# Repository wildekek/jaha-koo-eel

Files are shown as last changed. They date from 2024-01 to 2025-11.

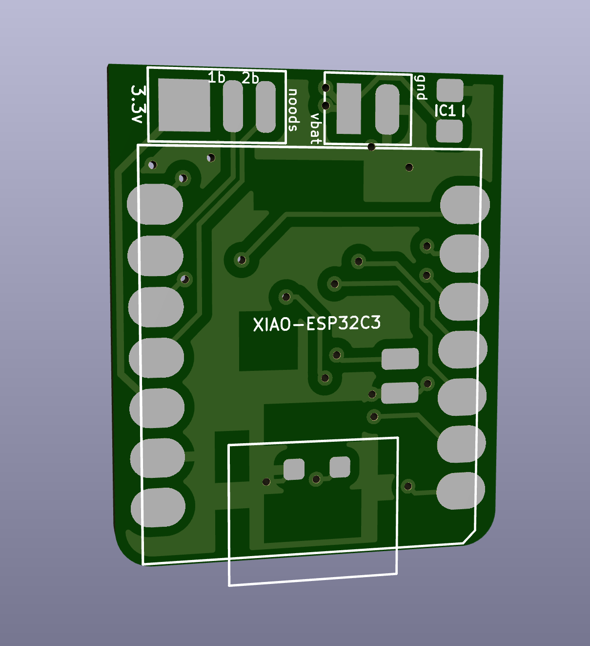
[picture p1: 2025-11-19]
kicad/eel_head_pcbs_assembly/eel_esp32_switch_host_board_v02/_export/images/HariboKimchi Eel mainboard - front.png

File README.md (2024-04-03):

# Jaha Koo Eel

A robotic remote controlled eel. A prop for the play [Haribo Kimchi](https://www.campo.nu/en/production/24342/haribo_kimchi).

A collaboration between [Adriaan Wormgoor](http://adriaanwormgoor.nl) and [Willem Vooijs](https://willem.vooijs.eu), produced for [Stichting Theater Utrecht](https://www.theaterutrecht.nl/innovationlab) and [Campo](https://campo.nu).

haribo

## Build your own
[Bill of Materials](./BOM.md)

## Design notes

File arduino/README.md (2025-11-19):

# Arduino code

All sketches where developed in `VSCode` using the `Platformio` extension.

There's a _lot_ of scrappy test sketches, so find below a quick link to the most recent version of key sketches.

### Main sketch for Eel microcontroller (XIAO ESP32-C3)

[main_seeed_xiao_esp32c3_v2_w_external_files.cpp](./platformio/esp32c3_helloworld/esp32c3_helloworld/src/main_seeed_xiao_esp32c3_v2_w_external_files.cpp)

### Main sketch for Teensy 3.2 inside the GEPRC Tinyradio r/c transmitter

[main.cpp](./platformio/TeensyDuino/src/main.cpp)

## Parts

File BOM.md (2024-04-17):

# Bill Of Materials

## 3Print files

> 💡 Print all these files in PETG

| Quantity | Model | Color |
| --- | --- | --- |
| 1 | Motor Mount | Transparent  |
| 1 | Head Upper | Transparent  |
| 1 | Head Lower | Transparent  |
| 1 | Switch cap | Transparent  |
| 2 | Eye Light Guide | Black |
| 2 | Mouth Light Guide | Black |
| 2 | Front Wheel | Transparent  |
| 1 | Tail | Transparent  |
| 19 | Segment | Transparent  |
| 8 | Segment with n00d | Transparent  |
| 1 | Segment battery | Transparent  |
| 4 | Axle | Transparent  |
| 8 | Wheel | Transparent  |

## Components

| Quantity | Component | Comments |
| --- | --- | --- |
| 8 | O-ring for wheels | Transparent silicone  |
| 2 | O-ring for front wheels | Transparent silicone  |

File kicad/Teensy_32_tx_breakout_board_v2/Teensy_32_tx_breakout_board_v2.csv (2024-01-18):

Source: | /Users/adriaanwormgoor/datkanarie/projects/Theater Utrecht - Jaha Koo Eel/Jaha Koo Eel - git/kicad/Teensy_32_tx_breakout_board/Teensy_32_tx_breakout_board.kicad_sch
Date: | 2024 January 09, Tuesday 16:21:45
Tool: | Eeschema (6.0.5-0)
Generator: | /Applications/KiCad/KiCad.app/Contents/SharedSupport/plugins/bom_csv_grouped_by_value_with_fp.py
Component Count: | 11
Ref | Qnty | Value | Cmp name | Footprint | Description | Vendor
C1, C2, C3, | 3 | 1uf | C | Capacitor_SMD:C_0603_1608Metric | Unpolarized capacitor
J1, J2, J3, J4, | 4 | Conn_01x03_Female | Conn_01x03_Female | Connector_JST:JST_SH_BM03B-SRSS-TB_1x03-1MP_P1.00mm_Vertical | Generic connector, single row, 01x03, script generated (kicad-library-utils/schlib/autogen/connector/)
R1, R2, R3, | 3 | 10k | R | Resistor_SMD:R_0603_1608Metric | Resistor
U1, | 1 | Teensy3.2_backpack | Teensy3.2_backpack | teensy_library-master:Teensy30_31_32_outside_pins

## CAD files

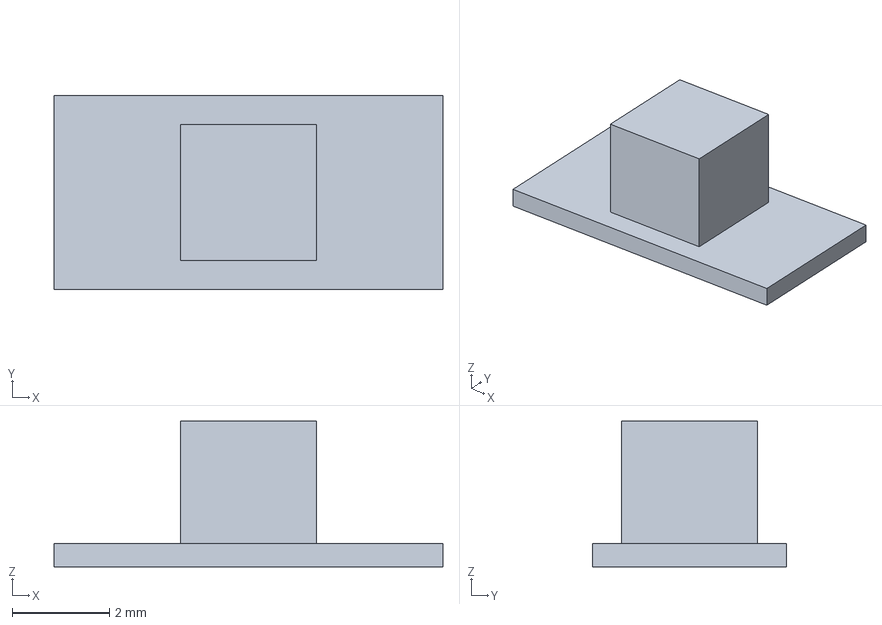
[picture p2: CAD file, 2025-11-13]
CAD/3mf/Main pcb slide switch end cap.3mf
8.00 x 4.00 x 3.00 mm

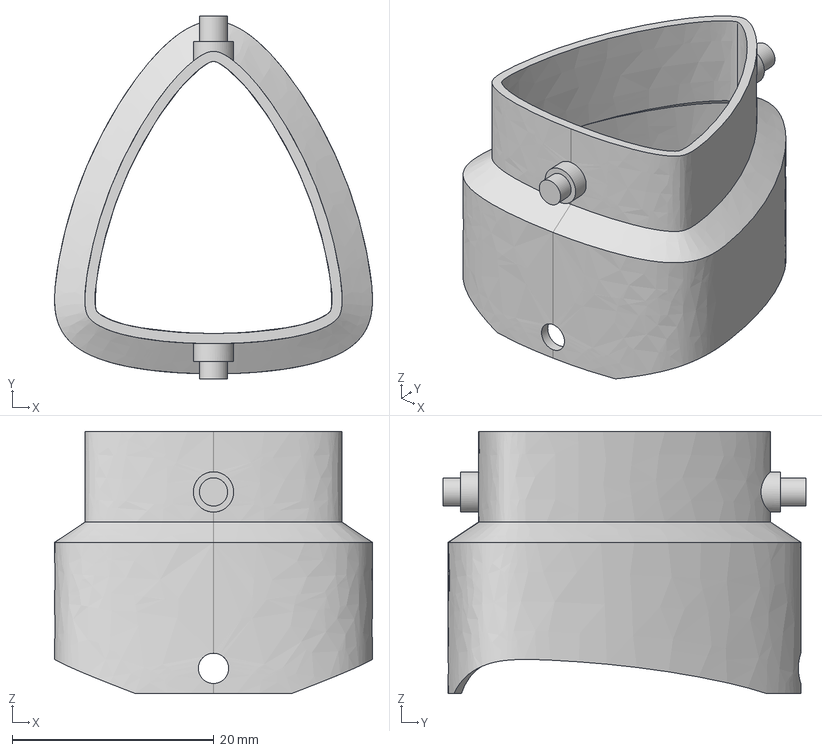
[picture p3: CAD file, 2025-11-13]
CAD/Haribo.step
31.5 x 36.0 x 26.0 mm

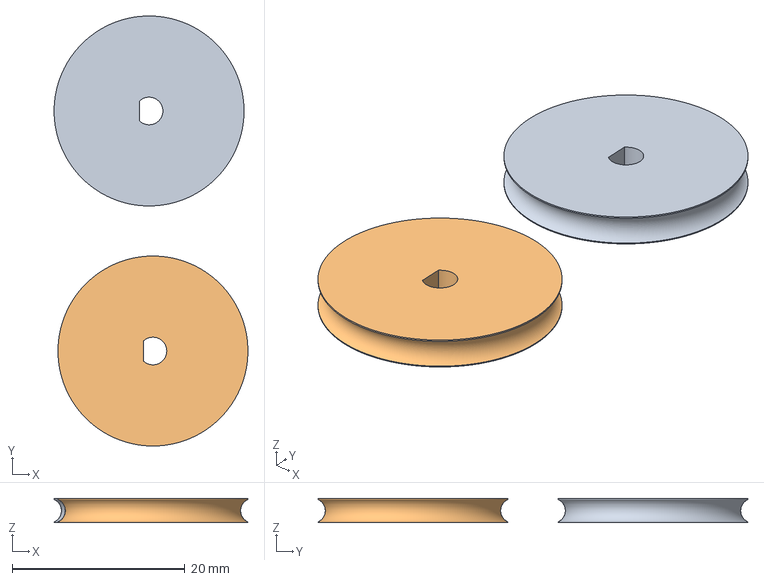
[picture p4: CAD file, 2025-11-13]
CAD/3mf/motor wheel v01.3mf
22.4 x 49.8 x 2.80 mm

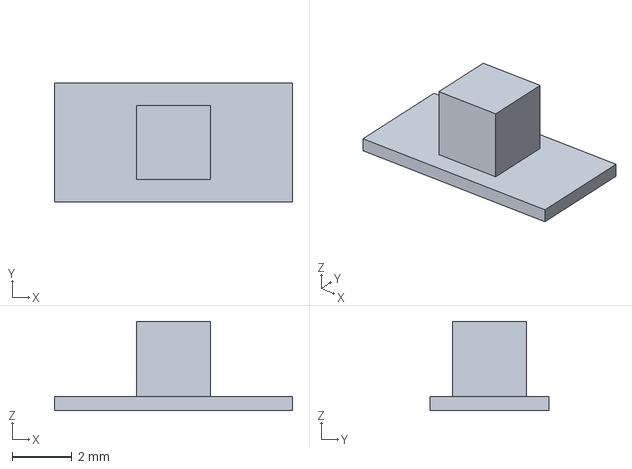
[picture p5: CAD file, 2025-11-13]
CAD/3mf/Switch cap .3mf
8.00 x 4.00 x 3.00 mm

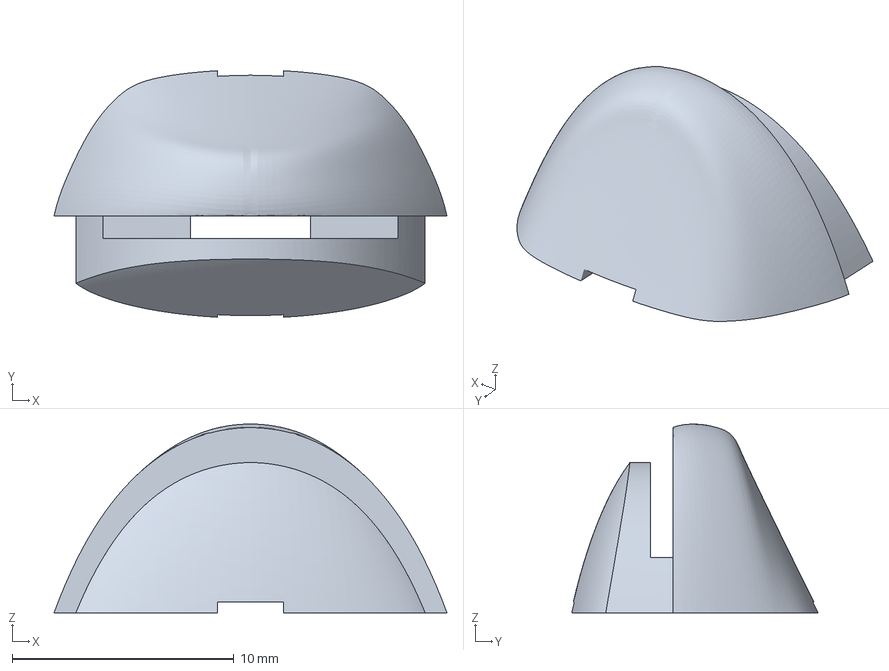
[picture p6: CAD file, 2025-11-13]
CAD/3mf/Mouth Light Guide.3mf
17.7 x 11.1 x 8.52 mm

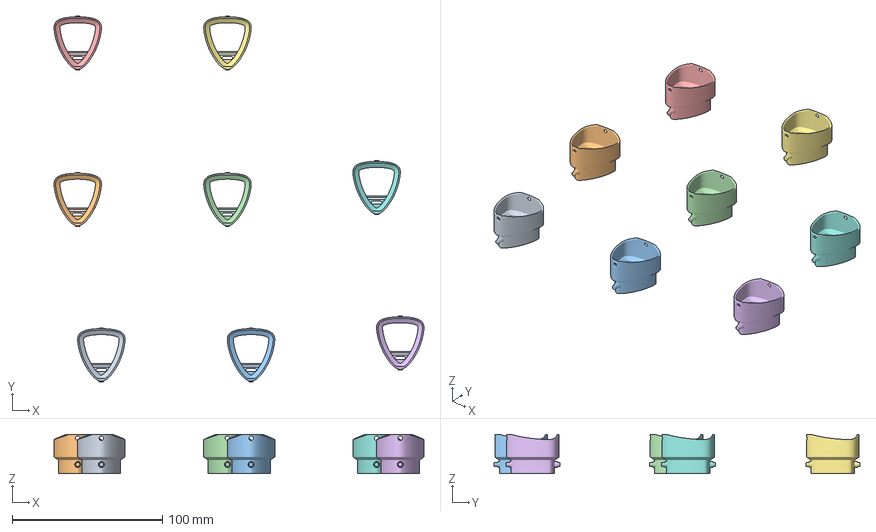
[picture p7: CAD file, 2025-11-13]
CAD/3mf/Segment with n00d.3mf
246.0 x 243.3 x 26.0 mm
Segment (1)
Segment (1) 1 x 2
Segment (1) 2
Segment (1) 3
Segment (1) 4
Segment (1) 5
Segment (1) 6

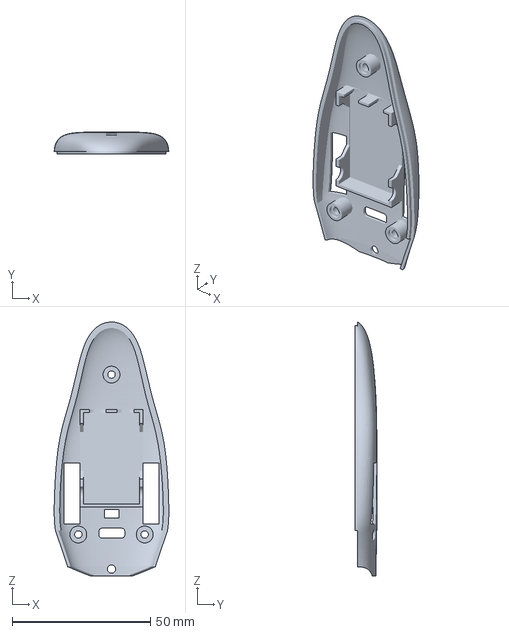
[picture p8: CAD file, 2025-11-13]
CAD/3mf/Head Lower.3mf
41.4 x 8.04 x 91.8 mm

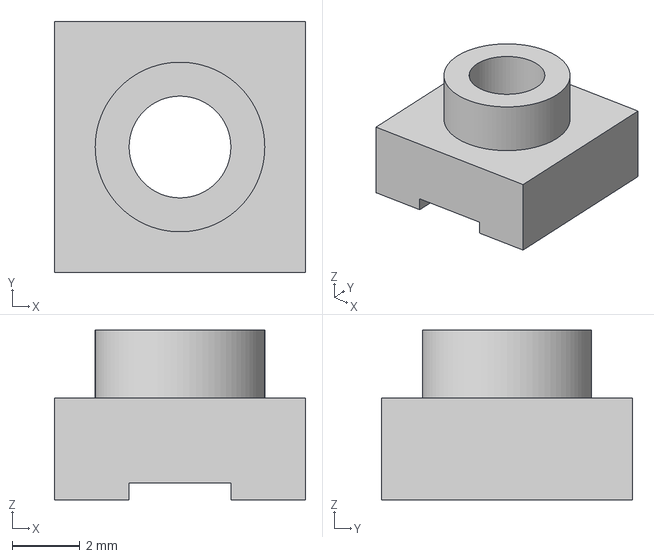
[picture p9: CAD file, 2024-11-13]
CAD/3mf/Eye Light Guide.3mf
7.40 x 7.40 x 5.00 mm

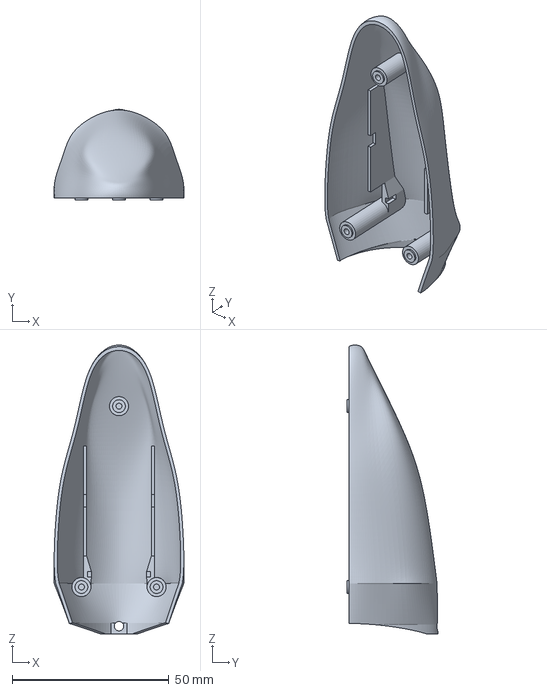
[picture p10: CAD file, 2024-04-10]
CAD/3mf/Head Upper.3mf
41.5 x 28.9 x 92.3 mm

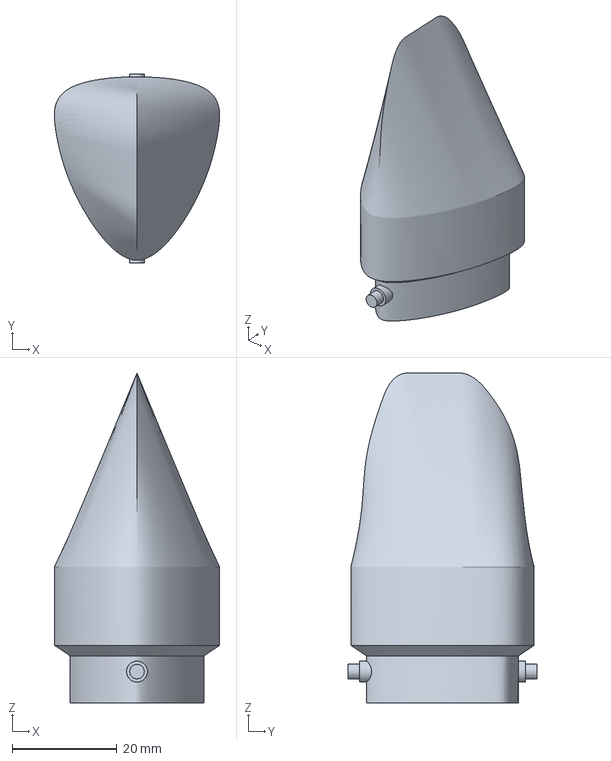
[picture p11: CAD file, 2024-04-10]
CAD/3mf/Tail.3mf
31.5 x 36.0 x 63.0 mm

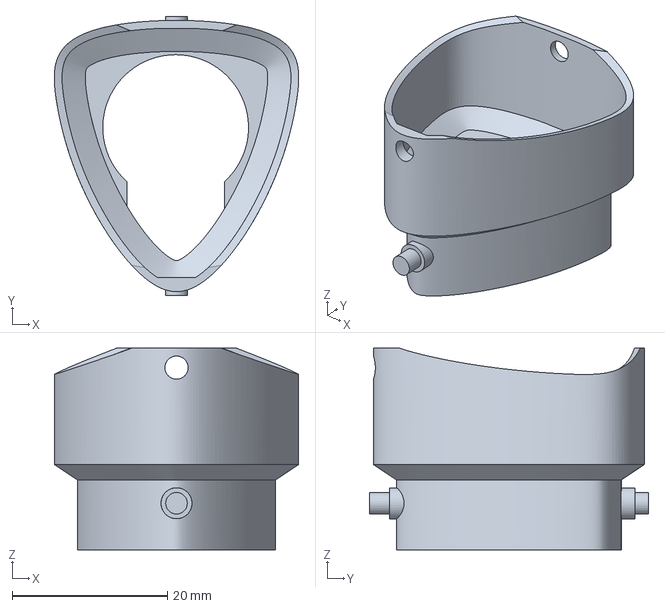
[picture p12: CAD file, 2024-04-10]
CAD/3mf/Segment Battery.3mf
31.5 x 36.0 x 26.0 mm

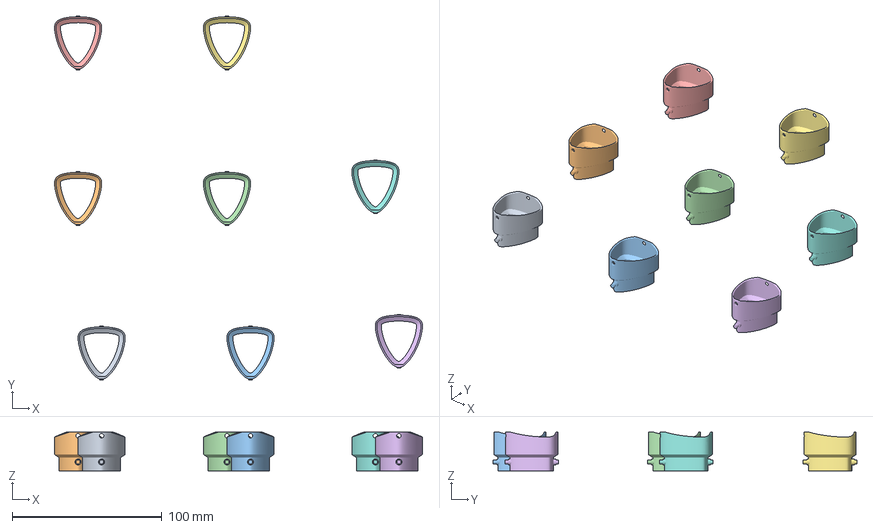
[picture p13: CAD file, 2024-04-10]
CAD/3mf/Segment.3mf
246.0 x 243.3 x 26.0 mm
Segment (1)
Segment (1) 1
Segment (1) 2
Segment (1) 3
Segment (1) 4
Segment (1) 5
Segment (1) 6
Segment (1) 7

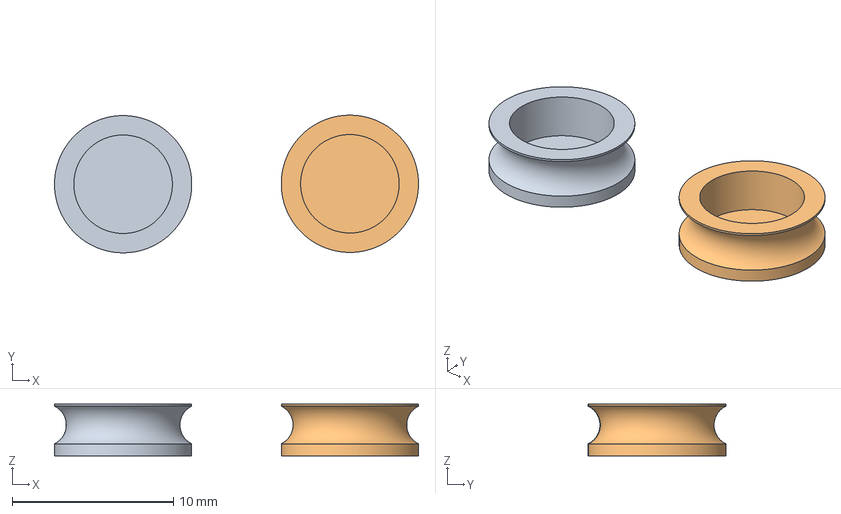
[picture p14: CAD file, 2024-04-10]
CAD/3mf/undercarriage wheel.3mf
22.5 x 8.53 x 3.20 mm
ball bearing wheel cover (with o-ring slot) v07 slightly tighter (2024-04-08).stl x 2

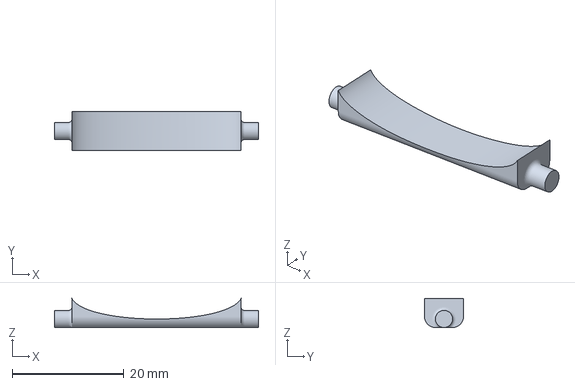
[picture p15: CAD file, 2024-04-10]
CAD/3mf/undercarriage axle.3mf
36.5 x 7.00 x 5.20 mm

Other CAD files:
CAD/3mf/Motor Mount.3mf

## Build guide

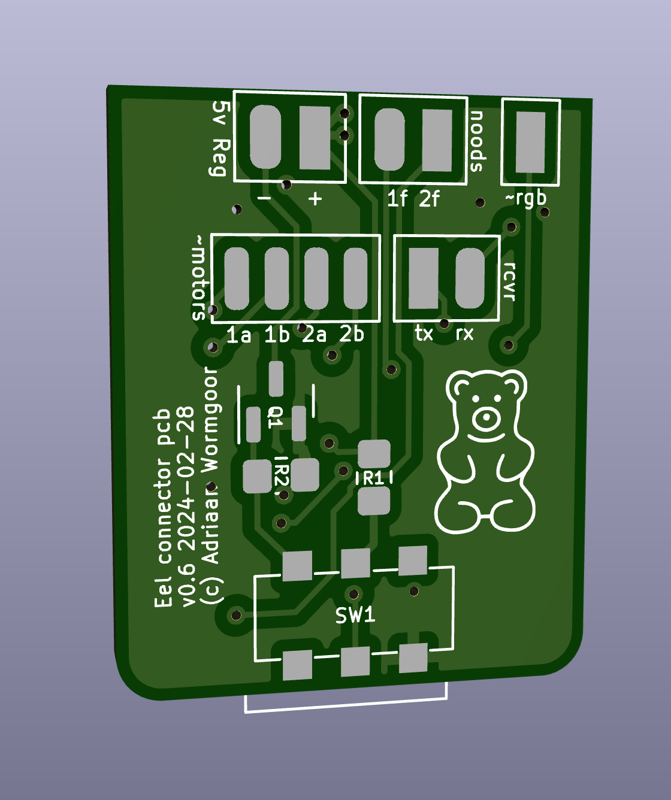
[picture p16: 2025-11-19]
kicad/eel_head_pcbs_assembly/eel_esp32_switch_host_board_v02/_export/images/HariboKimchi Eel mainboard - back.png

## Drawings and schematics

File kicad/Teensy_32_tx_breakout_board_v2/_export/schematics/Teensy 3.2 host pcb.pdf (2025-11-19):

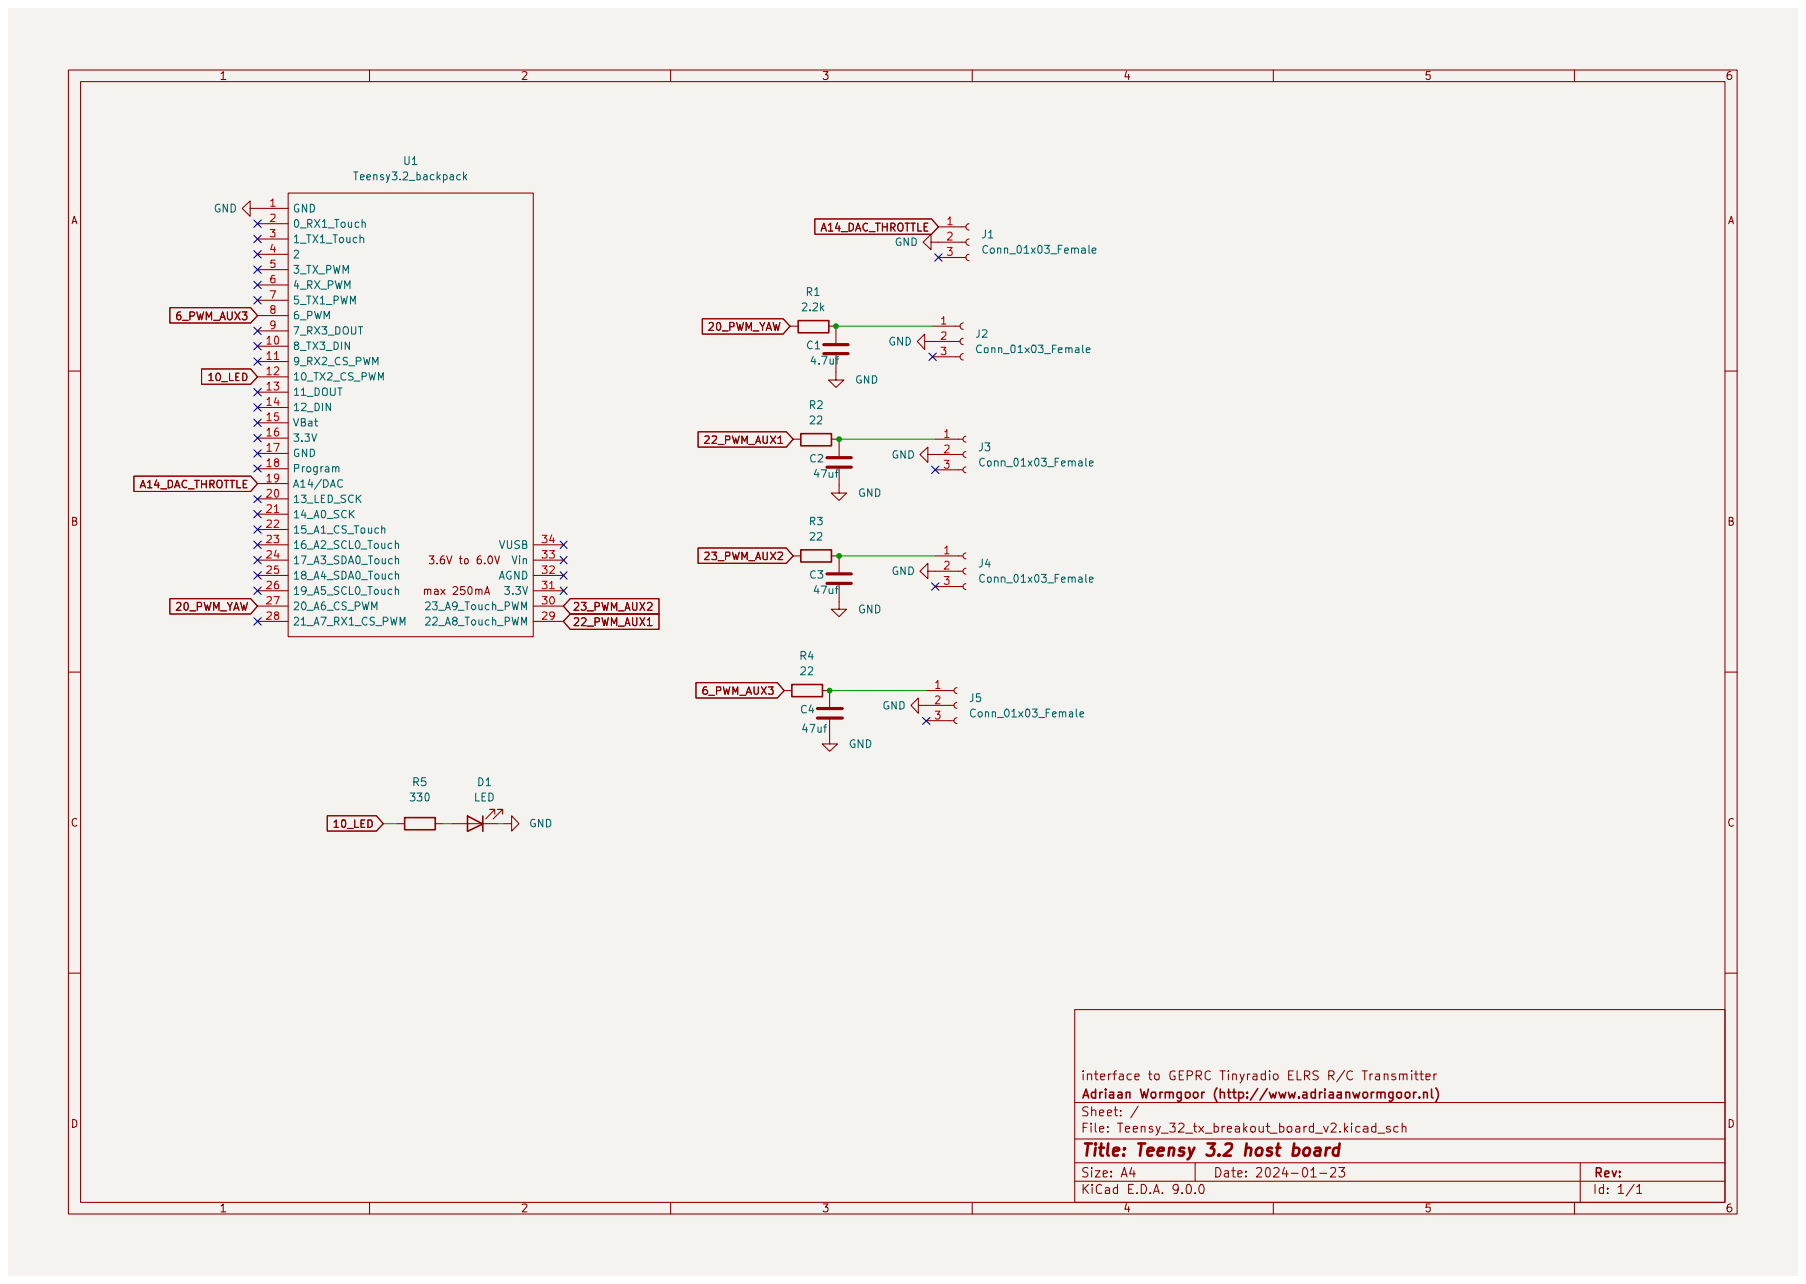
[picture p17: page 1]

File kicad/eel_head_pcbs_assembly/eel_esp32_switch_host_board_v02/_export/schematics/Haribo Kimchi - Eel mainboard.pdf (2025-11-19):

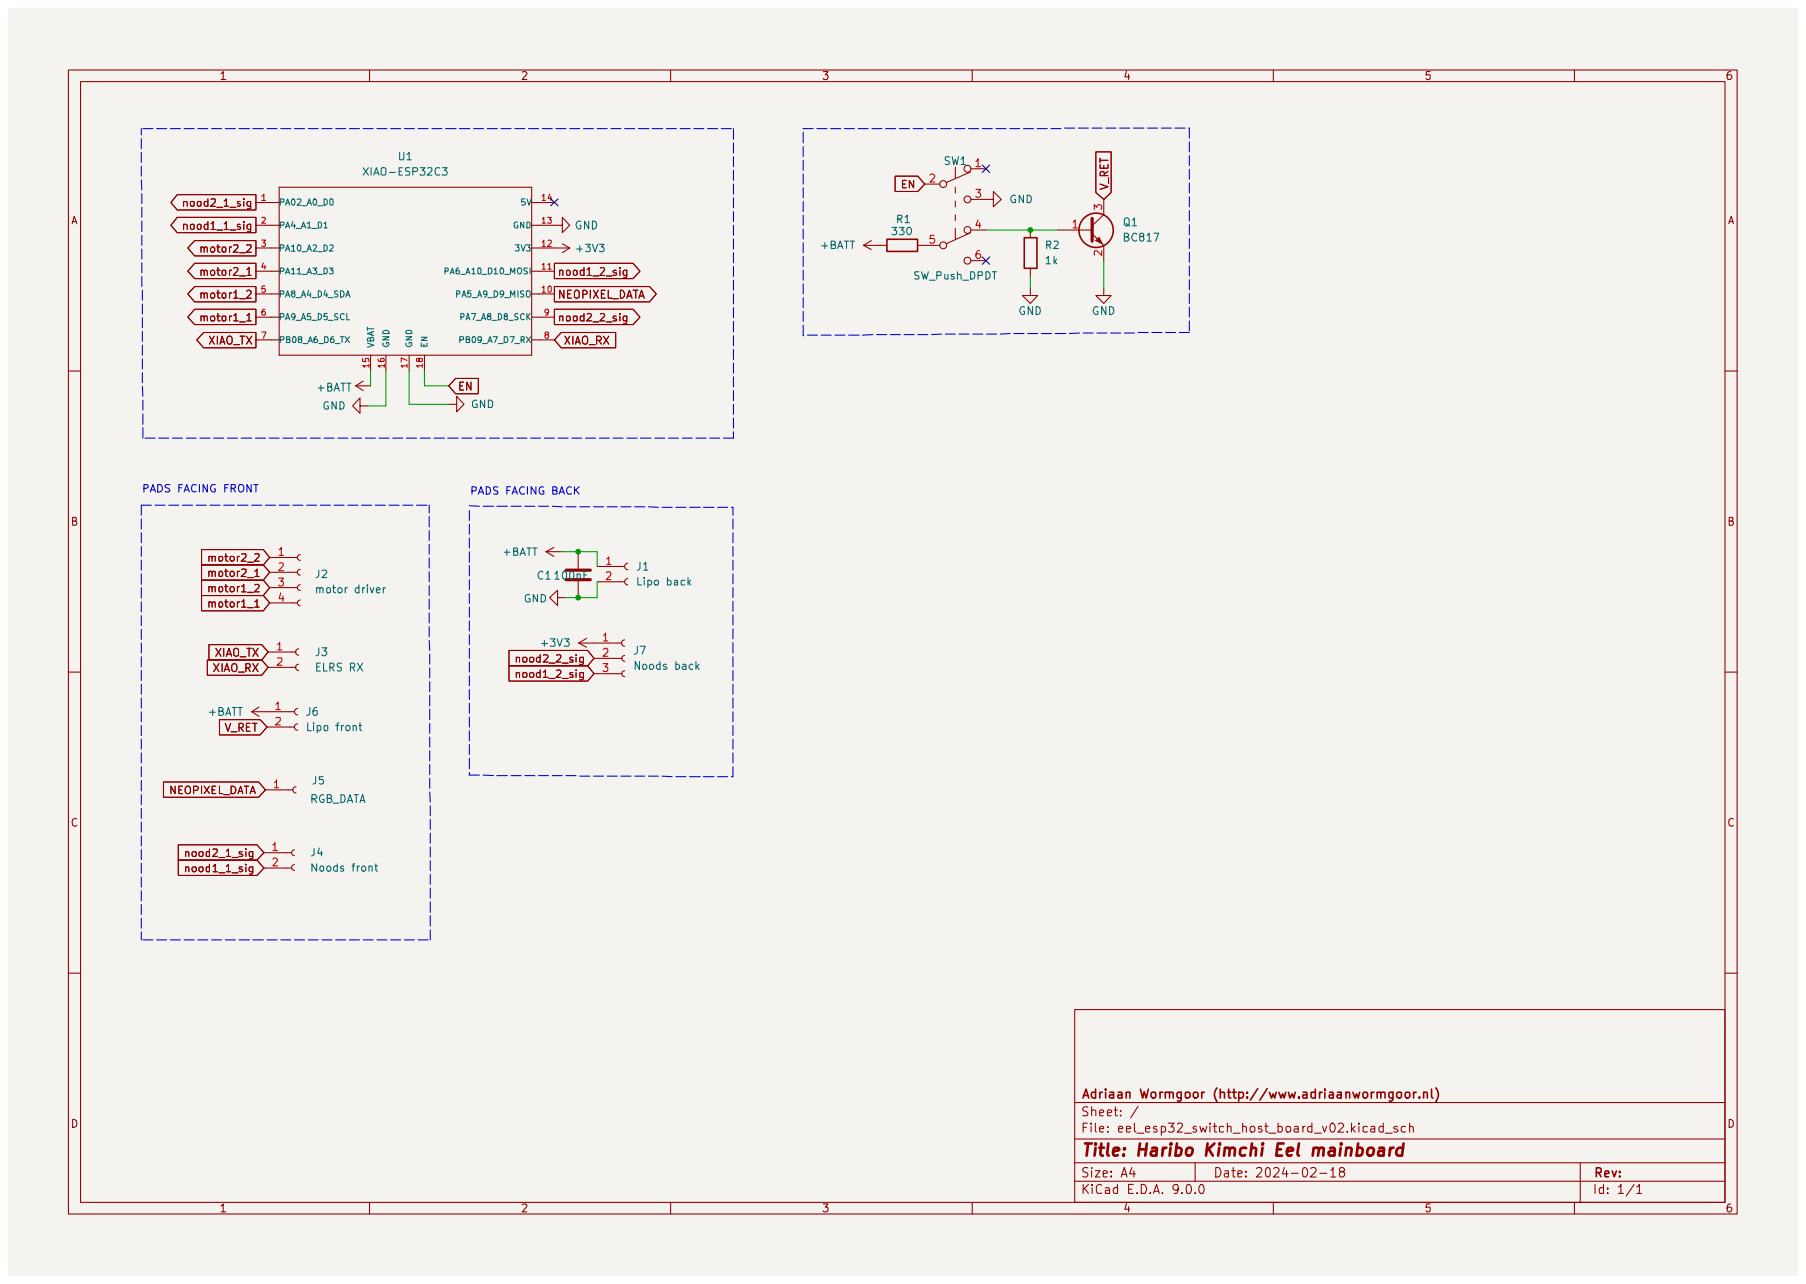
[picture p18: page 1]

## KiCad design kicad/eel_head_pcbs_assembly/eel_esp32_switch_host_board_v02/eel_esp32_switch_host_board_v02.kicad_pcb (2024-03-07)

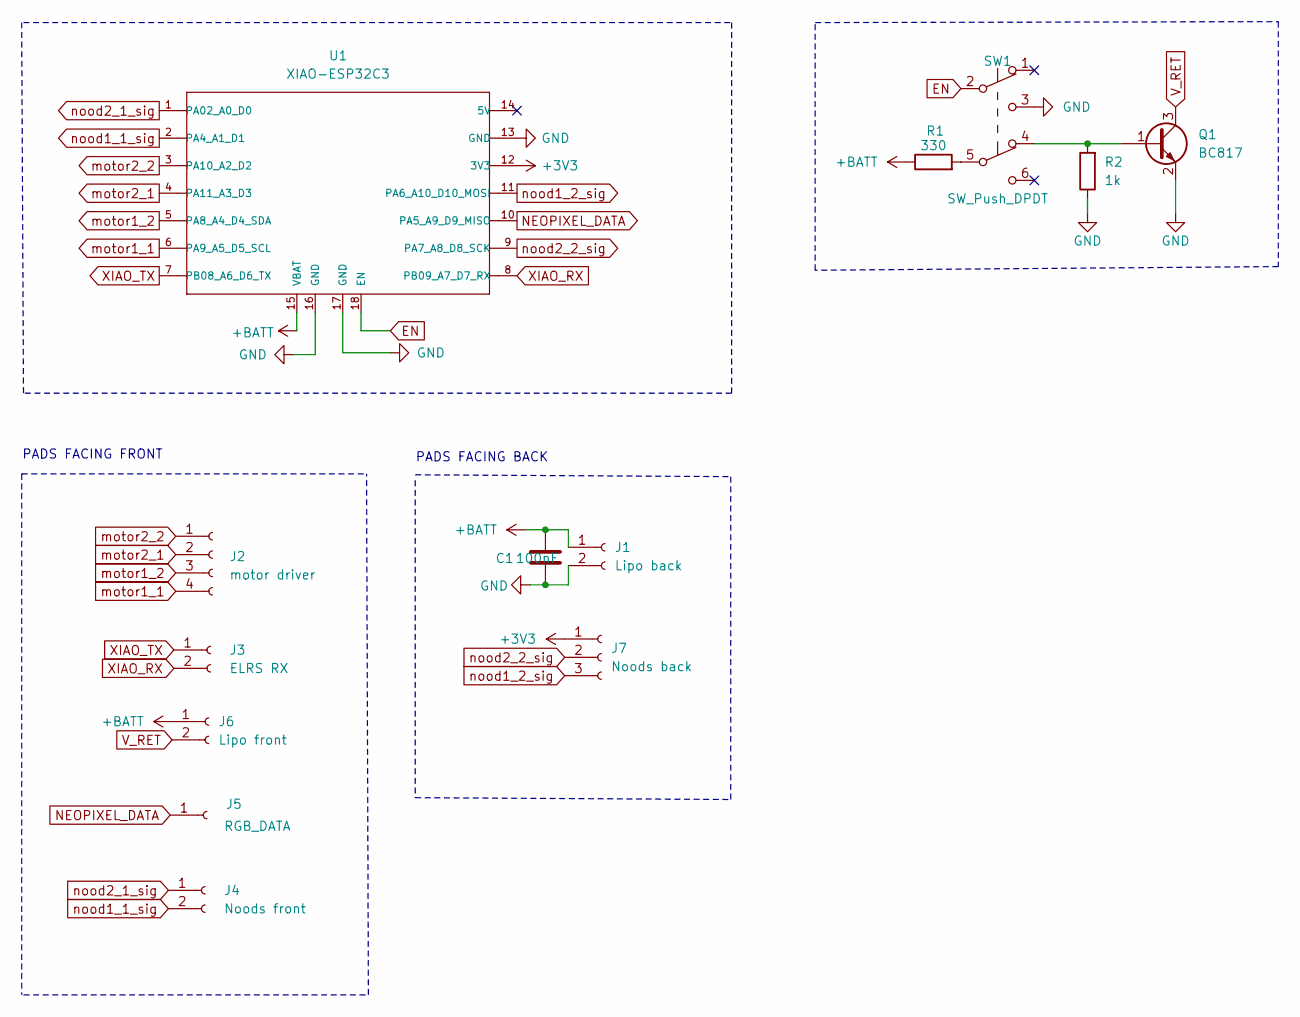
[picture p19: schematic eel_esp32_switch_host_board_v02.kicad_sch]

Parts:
C1: 100nF; C_0805_2012Metric_Pad1.18x1.45mm_HandSolder
J1: Lipo back; smd_solder_pads_1x02_2.54mm
J2: motor driver; smd_solder_pads_1x04
J3: ELRS RX; smd_solder_pads_1x02_2.54mm
J4: Noods front; smd_solder_pads_1x02_2.54mm
J5: RGB_DATA; smd_solder_pads_1x01_2.54mm
J6: Lipo front; smd_solder_pads_1x02_2.54mm
J7: Noods back; smd_solder_pads_1x03_n00ds_v1
Q1: BC817; SOT-23
R1: 330; R_0805_2012Metric_Pad1.20x1.40mm_HandSolder
R2: 1k; R_0805_2012Metric_Pad1.20x1.40mm_HandSolder
SW1: SW_Push_DPDT; Nidec_2x03_dpdt_CL-SB-22B-11
U1: XIAO-ESP32C3; MOUDLE14P-SMD-2.54-21X17.8MM

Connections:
+3V3: J7.1, U1.12 (3V3)
+BATT: C1.1, J1.1, J6.1, R1.1, U1.15 (VBAT)
EN: SW1.2 (B), U1.18 (EN)
GND: C1.2, J1.2, Q1.2 (E), R2.1, SW1.3 (C), U1.13 (GND), U1.16 (GND), U1.17 (GND)
NEOPIXEL_DATA: J5.1, U1.10 (PA5_A9_D9_MISO)
unnamed: Q1.1 (B), R2.2, SW1.4 (A)
unnamed: R1.2, SW1.5 (B)
V_RET: J6.2, Q1.3 (C)
XIAO_RX: J3.2, U1.8 (PB09_A7_D7_RX)
XIAO_TX: J3.1, U1.7 (PB08_A6_D6_TX)
motor1_1: J2.4, U1.6 (PA9_A5_D5_SCL)
motor1_2: J2.3, U1.5 (PA8_A4_D4_SDA)
motor2_1: J2.2, U1.4 (PA11_A3_D3)
motor2_2: J2.1, U1.3 (PA10_A2_D2)
nood1_1_sig: J4.2, U1.2 (PA4_A1_D1)
nood1_2_sig: J7.3, U1.11 (PA6_A10_D10_MOSI)
nood2_1_sig: J4.1, U1.1 (PA02_A0_D0)
nood2_2_sig: J7.2, U1.9 (PA7_A8_D8_SCK)

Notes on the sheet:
PADS FACING BACK
PADS FACING FRONT

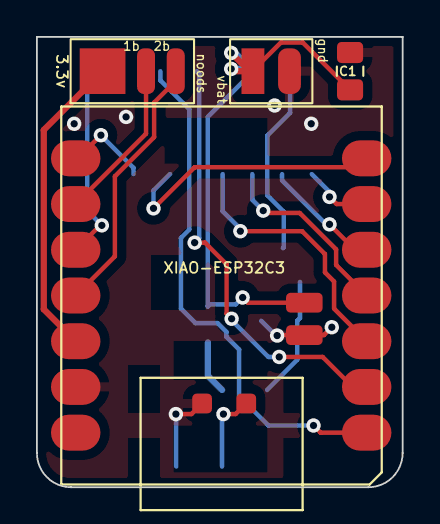
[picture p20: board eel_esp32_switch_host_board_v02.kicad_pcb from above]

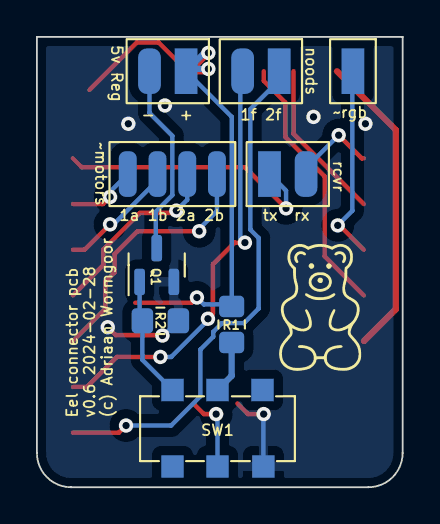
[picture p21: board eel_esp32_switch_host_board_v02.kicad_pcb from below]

Board: 2 copper layers, 20.3 x 25.0 mm, 13 parts (9 on the bottom side), 18 nets.

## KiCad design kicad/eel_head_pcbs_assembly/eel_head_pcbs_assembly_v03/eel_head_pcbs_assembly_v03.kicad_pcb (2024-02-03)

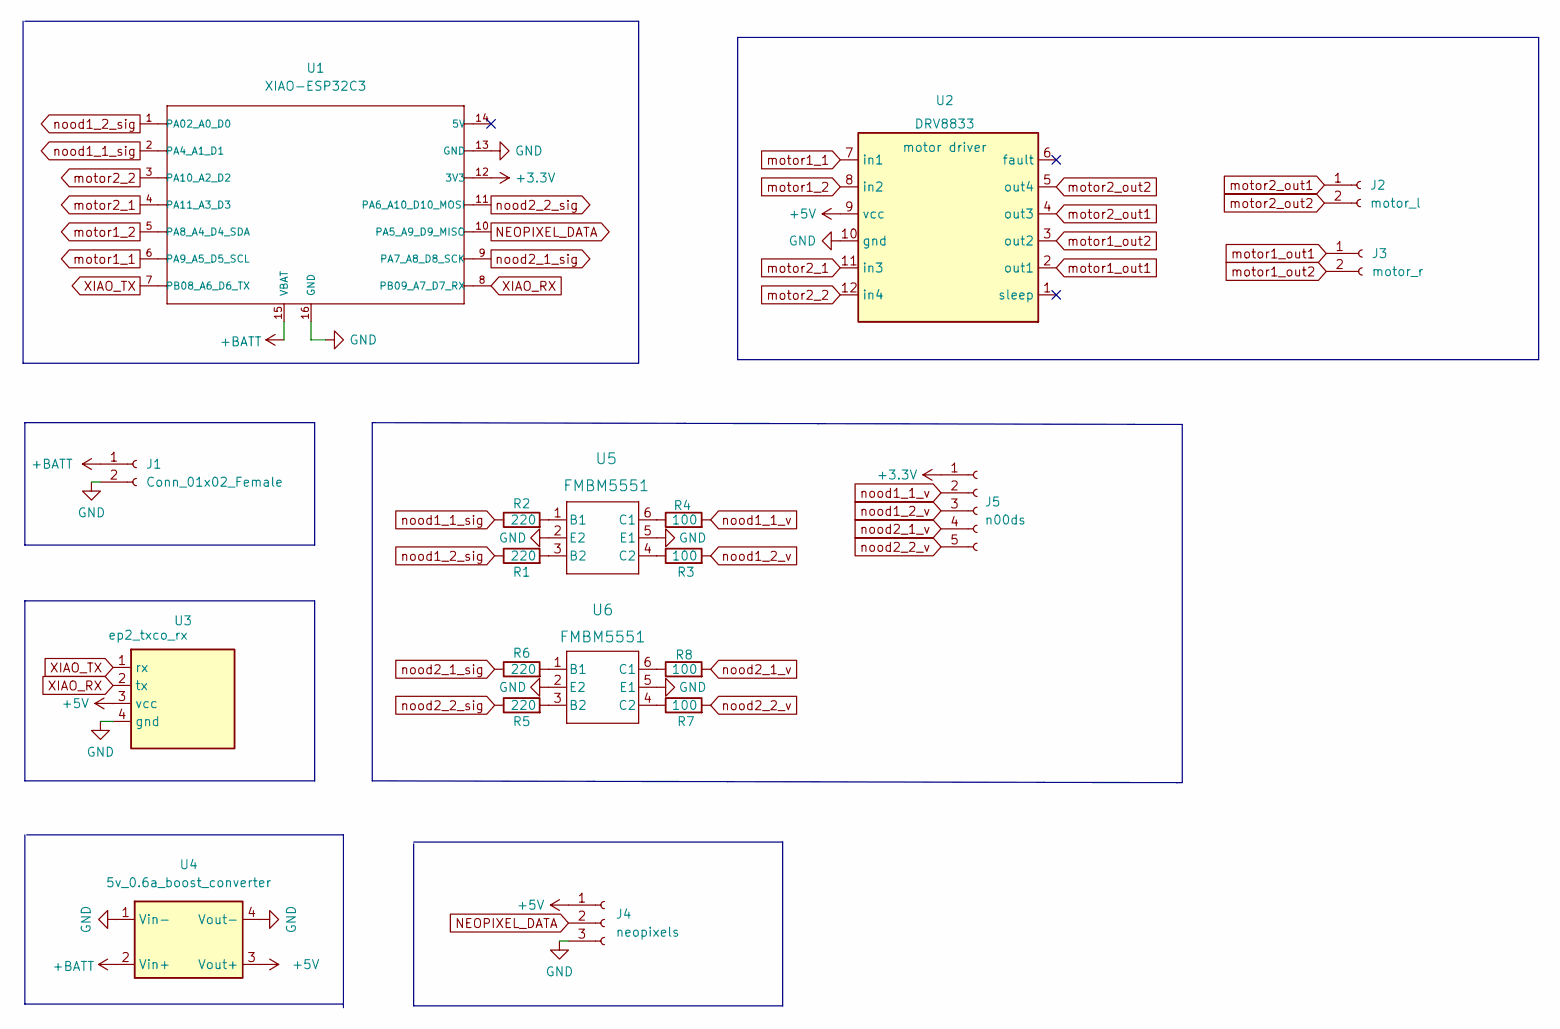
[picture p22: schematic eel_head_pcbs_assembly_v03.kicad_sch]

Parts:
J1: Conn_01x02_Female; JST_PH_S2B-PH-K_1x02_P2.00mm_Horizontal
J2: motor_l; smd_solder_pads_1x02_2.54mm
J3: motor_r; smd_solder_pads_1x02_2.54mm
J4: neopixels; smd_solder_pads_1x03_2.54mm
J5: n00ds; smd_solder_pads_1x05_n00ds_v2_smaller
R1, R2, R5, R6: 220; R_0603_1608Metric_Pad0.98x0.95mm_HandSolder
R3, R4, R7, R8: 100; R_0603_1608Metric_Pad0.98x0.95mm_HandSolder
U1: XIAO-ESP32C3; MOUDLE14P-SMD-2.54-21X17.8MM
U2: DRV8833; drv8833_breakout
U3: ep2_txco_rx; happymodel_ep2_txco_rx
U4: 5v_0.6a_boost_converter
U5, U6: FMBM5551; SSOT6_3X1P7_ONS

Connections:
+3V3: J5.1, U1.12 (3V3)
+5V: J4.1, U2.9 (vcc), U3.3 (vcc), U4.3 (Vout+)
+BATT: J1.1, U1.15 (VBAT), U4.2 (Vin+)
GND: J1.2, J4.3, U1.13 (GND), U1.16 (GND), U2.10 (gnd), U3.4 (gnd), U4.1 (Vin-), U4.4 (Vout-), U5.2 (E2), U5.5 (E1), U6.2 (E2), U6.5 (E1)
NEOPIXEL_DATA: J4.2, U1.10 (PA5_A9_D9_MISO)
unnamed: R1.2, U5.3 (B2)
unnamed: R2.2, U5.1 (B1)
unnamed: R3.1, U5.4 (C2)
unnamed: R4.1, U5.6 (C1)
unnamed: R5.2, U6.3 (B2)
unnamed: R6.2, U6.1 (B1)
unnamed: R7.1, U6.4 (C2)
unnamed: R8.1, U6.6 (C1)
XIAO_RX: U1.8 (PB09_A7_D7_RX), U3.2 (tx)
XIAO_TX: U1.7 (PB08_A6_D6_TX), U3.1 (rx)
motor1_1: U1.6 (PA9_A5_D5_SCL), U2.7 (in1)
motor1_2: U1.5 (PA8_A4_D4_SDA), U2.8 (in2)
motor1_out1: J3.1, U2.2 (out1)
motor1_out2: J3.2, U2.3 (out2)
motor2_1: U1.4 (PA11_A3_D3), U2.11 (in3)
motor2_2: U1.3 (PA10_A2_D2), U2.12 (in4)
motor2_out1: J2.1, U2.4 (out3)
motor2_out2: J2.2, U2.5 (out4)
nood1_1_sig: R2.1, U1.2 (PA4_A1_D1)
nood1_1_v: J5.2, R4.2
nood1_2_sig: R1.1, U1.1 (PA02_A0_D0)
nood1_2_v: J5.3, R3.2
nood2_1_sig: R6.1, U1.9 (PA7_A8_D8_SCK)
nood2_1_v: J5.4, R8.2
nood2_2_sig: R5.1, U1.11 (PA6_A10_D10_MOSI)
nood2_2_v: J5.5, R7.2

Board: 2 copper layers, 21 parts (15 on the bottom side), 31 nets, no tracks yet.

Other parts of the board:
haribo_korean: LOGO; haribo_in_korean_3.2mm
logo_haribo_bear: LOGO; haribo_outline_bw_8mm

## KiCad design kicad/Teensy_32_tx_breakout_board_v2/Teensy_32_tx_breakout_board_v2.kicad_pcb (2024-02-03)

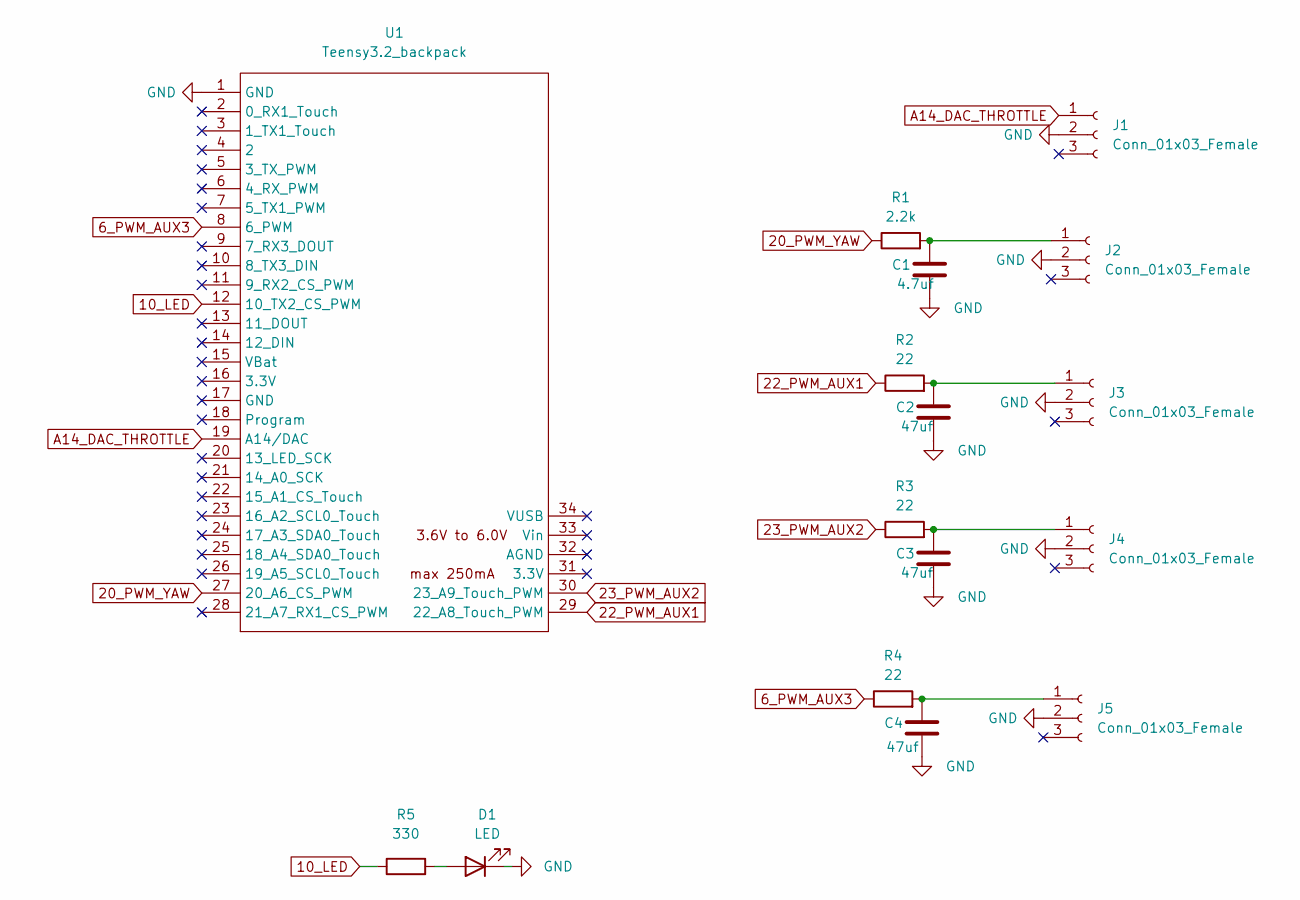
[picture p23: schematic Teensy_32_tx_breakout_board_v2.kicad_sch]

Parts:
C1: 4.7uf; C_0603_1608Metric
C2, C3, C4: 47uf; C_0603_1608Metric
D1: LED; LED_1206_3216Metric
J1, J2, J3, J4, J5: Conn_01x03_Female; JST_SH_BM03B-SRSS-TB_1x03-1MP_P1.00mm_Vertical
R1: 2.2k; R_0603_1608Metric
R2, R3, R4: 22; R_0603_1608Metric
R5: 330; R_1206_3216Metric
U1: Teensy3.2_backpack; Teensy30_31_32_outside_pins

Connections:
6_PWM_AUX3: R4.1, U1.8 (6_PWM)
10_LED: R5.1, U1.12 (10_TX2_CS_PWM)
20_PWM_YAW: R1.1, U1.27 (20_A6_CS_PWM)
22_PWM_AUX1: R2.1, U1.29 (22_A8_Touch_PWM)
23_PWM_AUX2: R3.1, U1.30 (23_A9_Touch_PWM)
A14_DAC_THROTTLE: J1.1, U1.19 (A14/DAC)
GND: C1.2, C2.2, C3.2, C4.2, D1.2 (K), J1.2, J2.2, J3.2, J4.2, J5.2, U1.1 (GND)
unnamed: C1.1, J2.1, R1.2
unnamed: C2.1, J3.1, R2.2
unnamed: C3.1, J4.1, R3.2
unnamed: C4.1, J5.1, R4.2
unnamed: D1.1 (A), R5.2

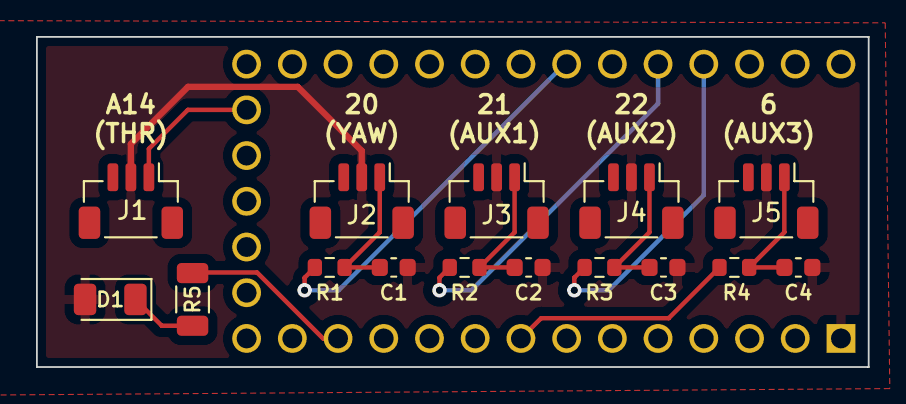
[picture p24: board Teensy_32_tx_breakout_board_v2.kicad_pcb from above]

Board: 2 copper layers, 46.2 x 18.3 mm, 16 parts (1 on the bottom side), 12 nets.

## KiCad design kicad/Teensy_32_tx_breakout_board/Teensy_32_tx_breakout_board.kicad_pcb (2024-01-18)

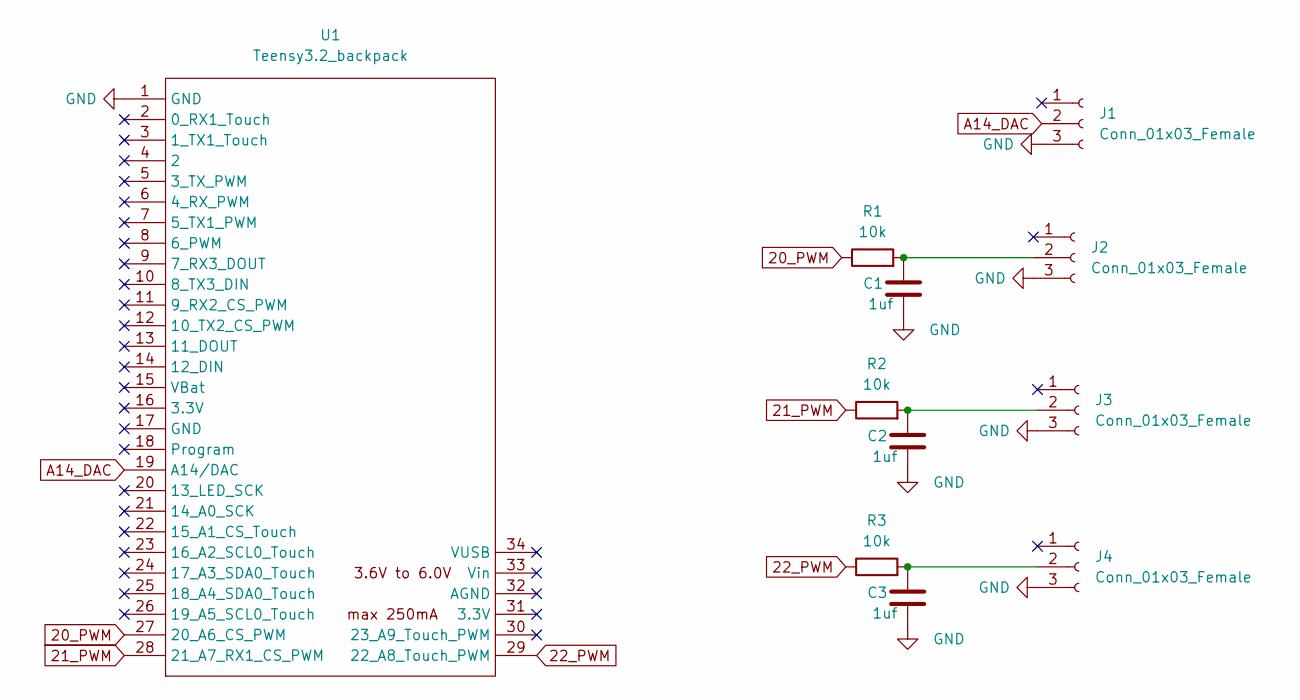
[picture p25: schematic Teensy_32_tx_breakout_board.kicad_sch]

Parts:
C1, C2, C3: 1uf; C_0603_1608Metric
J1, J2, J3, J4: Conn_01x03_Female; JST_SH_BM03B-SRSS-TB_1x03-1MP_P1.00mm_Vertical
R1, R2, R3: 10k; R_0603_1608Metric
U1: Teensy3.2_backpack; Teensy30_31_32_outside_pins

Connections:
20_PWM: R1.1, U1.27 (20_A6_CS_PWM)
21_PWM: R2.1, U1.28 (21_A7_RX1_CS_PWM)
22_PWM: R3.1, U1.29 (22_A8_Touch_PWM)
A14_DAC: J1.2, U1.19 (A14/DAC)
GND: C1.2, C2.2, C3.2, J1.3, J2.3, J3.3, J4.3, U1.1 (GND)
unnamed: C1.1, J2.2, R1.2
unnamed: C2.1, J3.2, R2.2
unnamed: C3.1, J4.2, R3.2

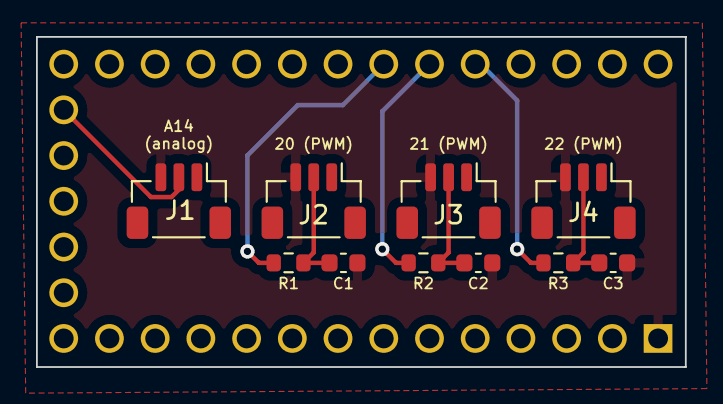
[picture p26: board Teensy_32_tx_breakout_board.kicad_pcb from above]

Board: 2 copper layers, 36.1 x 18.3 mm, 11 parts (1 on the bottom side), 8 nets.

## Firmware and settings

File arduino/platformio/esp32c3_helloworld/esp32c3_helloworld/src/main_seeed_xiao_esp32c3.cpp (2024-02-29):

#include <Arduino.h>
#include <EelMotor.h>
#include <Wire.h>
#include "sbus.h"
#include <HardwareSerial.h>
#include <Adafruit_NeoPixel.h>
#include <FastLED.h>

// NeoPixel
#define PIN D9
#define NUMPIXELS 3

// When setting up the NeoPixel library, we tell it how many pixels,
// and which pin to use to send signals. Note that for older NeoPixel
// strips you might need to change the third parameter -- see the
// strandtest example for more information on possible values.
Adafruit_NeoPixel pixels(NUMPIXELS, PIN, NEO_GRB + NEO_KHZ800);

HardwareSerial MySerial0(0);

/* SBUS object, reading SBUS */
bfs::SbusRx sbus_rx(&MySerial0, D7, D6, true, false);

/* SBUS data */
bfs::SbusData data;

#define motor1a_pin D5
#define motor1b_pin D4
#define motor2a_pin D3
#define motor2b_pin D2

#define motor1_chan 4 // 6 Channels (ESP32-C3) (0-5) are availible
#define motor2_chan 5 // 6 Channels (ESP32-C3) (0-5) are availible

// setting PWM properties
const uint32_t freq = 2500;
const uint8_t resolution = 8;

EelMotor motor1(motor1a_pin, motor1b_pin, motor1_chan, resolution, freq);
EelMotor motor2(motor2a_pin, motor2b_pin, motor2_chan, resolution, freq);

u_long sbusPrevPacketTime;
bool sbusLost = false;

#define SBUS_VAL_MIN 191
#define SBUS_VAL_MAX 1793
#define SBUS_VAL_CENTER 992
#define SBUS_VAL_DEADBAND 6
#define SBUS_LOST_TIMEOUT 100
#define SBUS_SWITCH_MIN 192
#define SBUS_SWITCH_MAX 1792
#define SBUS_SWITCH_MIN_THRESHOLD 1400
#define SBUS_SWITCH_MAX_THRESHOLD 550

#define TX_ROLL 0
#define TX_PITCH 1
#define TX_THROTTLE 2
#define TX_YAW 3
#define TX_AUX1 4
#define TX_AUX2 5
#define TX_AUX3 6
#define TX_AUX4 7

enum HEAD_STATE
{
  STATE_1,
  STATE_2
};
HEAD_STATE headState = STATE_1;

enum BODY_STATE
{
  NOOD1,
  NOOD2,
  BOTH_NOODS
};
BODY_STATE bodyState = BOTH_NOODS;

// The CONNECTION_ESTABLISHED and CONNECTION_LOST states are kind of vanity states, in case I want to
// implement some kind of unique visual feedback for when the connection is lost or established.
enum CONNECTION_STATE
{
  DISCONNECTED,
  CONNECTION_ESTABLISHED,
  CONNECTION_LOST,
  CONNECTED
};
CONNECTION_STATE connectionState = DISCONNECTED;

#define SBUS_PACKET_PRINT_INTERVAL 100 // ms
u_long sbusPacketPrintPrevTime = 0;

float sinCounter = 0.0;
float sinCounterIncrement = 0.05;

bool doSineMovement = false;

byte hVal = 0;
byte vVal = 0;

int16_t motor1Val;
int16_t motor2Val;

int16_t n00d1a, n00d1b, n00d2a, n00d2b;
uint16_t throttle, throttleAdjusted;

int16_t noodVals[] = {0, 0, 0, 0};
int16_t noodAvgVals[] = {0, 0, 0, 0};
uint16_t n00dSegmentIdentifiers[] = {512, 640, 768, 896};

#define n00d_1a_Pin D1
#define n00d_1b_Pin D10
#define n00d_2a_Pin D0
#define n00d_2b_Pin D8

static const uint8_t nood1a_chan = 0;
static const uint8_t nood1b_chan = 1;
static const uint8_t nood2a_chan = 2;
static const uint8_t nood2b_chan = 3;

void initNoods();
void initPixels();
void updateBodyValues();
void updateBodyLighting();
void updateSerialIO();
void checkIncomingSerial();
void setn00d(uint8_t chan, uint8_t val);

void resetSbusData();
void setLights_disconnected();

// define methods
void driveMotors();
void parseSBUS(bool serialPrint);
void updateHeadBodyState();
void updateHeadLighting();
void updateBodyLighting();
void calcMotorValues();

void setup()
{
  Serial.begin(115200);

  /* Begin the SBUS communication */
  sbus_rx.Begin();
  // sbus_tx.Begin();

  /* not sure if this is necessary...
  ledcDetachPin(n00d_1a_Pin);
  ledcDetachPin(n00d_1b_Pin);
  ledcDetachPin(motor1a_pin);
  ledcDetachPin(motor1a_pin);
  ledcDetachPin(motor1b_pin);
  ledcDetachPin(motor2a_pin);
  ledcDetachPin(motor2b_pin);
  //*/

  initNoods();

  motor1.reversed = true;
  motor2.reversed = false;

  // by default, let's have the program assume sbus is lost
  sbusPrevPacketTime = -SBUS_LOST_TIMEOUT;

  initPixels();

  Serial.println("Hello World!");
}

void loop()
{
  // pixels.clear(); // Set all pixel colors to 'off'

  // read SBUS
  parseSBUS(true);

  // determine how to set the head and body lights
  switch (connectionState) {
    case DISCONNECTED:
      resetSbusData();
      setLights_disconnected();
      break;
    case CONNECTION_ESTABLISHED:
      if (sbusLost) {
        connectionState = CONNECTION_LOST;
      } else {
        connectionState = CONNECTED;
      }
      break;
    case CONNECTION_LOST:
      if (!sbusLost) {
        connectionState = CONNECTION_ESTABLISHED;
      }
      break;
    case CONNECTED:
      if (sbusLost) {
        connectionState = CONNECTION_LOST;
      }
      break;
  }

  updateHeadBodyState();

  updateBodyValues();
  updateBodyLighting();

  updateHeadLighting();
  // updateBodyLighting();

  calcMotorValues();
  driveMotors();

  // delay a little.
  delay(1000 / 200);
}

void initNoods()
{
  pinMode(n00d_1a_Pin, OUTPUT);
  pinMode(n00d_1b_Pin, OUTPUT);
  pinMode(n00d_2a_Pin, OUTPUT);
  pinMode(n00d_2b_Pin, OUTPUT);

  // nood 1a
  ledcSetup(nood1a_chan, freq, resolution);
  ledcAttachPin(n00d_1a_Pin, nood1a_chan);

  // nood 1b
  ledcSetup(nood1b_chan, freq, resolution);
  ledcAttachPin(n00d_1b_Pin, nood1b_chan);

  // nood 2a
  ledcSetup(nood2a_chan, freq, resolution);
  ledcAttachPin(n00d_2a_Pin, nood2a_chan);

  // nood 2b
  ledcSetup(nood2b_chan, freq, resolution);
  ledcAttachPin(n00d_2b_Pin, nood2b_chan);

  setn00d(nood1a_chan, 0);
  setn00d(nood1b_chan, 0);
  setn00d(nood2a_chan, 0);
  setn00d(nood2b_chan, 0);
}

void initPixels() {
  pixels.begin(); // INITIALIZE NeoPixel strip object (REQUIRED)
  delay(10);
  pixels.clear();
  pixels.show();
}

void updateBodyValues()
{
  // map throttle range to 0-1023
  throttle = map(data.ch[TX_THROTTLE], SBUS_VAL_MIN, SBUS_VAL_MAX, 0, 1023);

  throttleAdjusted = 0; // used to store the adjusted throttle value

  // if (throttle & (0x1 << 9)) // 512
  // if (throttle & n00dSegmentIdentifiers[0] == n00dSegmentIdentifiers[0]) // 512
  if (throttle >> 7 == 0x4) // 0b100
  {
    // throttleAdjusted = throttle - (throttle >> 5);
    throttleAdjusted = throttle - 9;
    n00d1a = (throttle & 0x7E) - 9;
    n00d1a = map(constrain(n00d1a, 0, 55), 0, 55, 0, 255);
  }
  // if (throttle & (0x1 << 8)) // 256
  // if (throttle & n00dSegmentIdentifiers[1] == n00dSegmentIdentifiers[1]) // 640
  if (throttle >> 7 == 0x5) // 0b101
  {
    // throttle -= throttle - (throttle >> 5);
    throttleAdjusted = throttle - 10;
    n00d1b = (throttle & 0x7E) - 10;
    n00d1b = map(constrain(n00d1b, 0, 55), 0, 55, 0, 255);
  }
  // if (throttle & (0x1 << 7)) // 128
  // if (throttle & n00dSegmentIdentifiers[2] == n00dSegmentIdentifiers[2]) // 768
  if (throttle >> 7 == 0x6) // 0b110
  {
    throttleAdjusted = throttle - 9;
    n00d2a = (throttle & 0x7E) - 9;
    n00d2a = map(constrain(n00d2a, 0, 55), 0, 55, 0, 255);
  }
  // if (throttle & (0x1 << 6)) // 64
  // if (throttle & n00dSegmentIdentifiers[3] == n00dSegmentIdentifiers[3]) // 896
  if (throttle >> 7 == 0x7) // 0b111
  {
    throttleAdjusted = throttle - 9;
    n00d2b = (throttle & 0x7E) - 9;
    n00d2b = map(constrain(n00d2b, 0, 55), 0, 55, 0, 255);
  }

  noodVals[0] = n00d1a;
  noodVals[1] = n00d1b;
  noodVals[2] = n00d2a;
  noodVals[3] = n00d2b;    

  noodAvgVals[0] = 0.85 * noodAvgVals[0] + 0.15 * noodVals[0];
  noodAvgVals[1] = 0.85 * noodAvgVals[1] + 0.15 * noodVals[1];
  noodAvgVals[2] = 0.85 * noodAvgVals[2] + 0.15 * noodVals[2];
  noodAvgVals[3] = 0.85 * noodAvgVals[3] + 0.15 * noodVals[3];
}

void updateBodyLighting()
{
  setn00d(nood1a_chan, noodAvgVals[0]);
  setn00d(nood1b_chan, noodAvgVals[1]);
  setn00d(nood2a_chan, noodAvgVals[2]);
  setn00d(nood2b_chan, noodAvgVals[3]);
}

uint8_t channelToPrint = 255;
void updateSerialIO()
{
  checkIncomingSerial();

  EVERY_N_MILLIS(100)
  {
    if (channelToPrint == 0) // only nood1a
    {
      Serial.print("n00d1a: ");
      Serial.print(n00d1a);
      Serial.print("\t in binary: ");
      Serial.println(n00d1a, BIN);
    }
    if (channelToPrint == 1) // only nood1b
    {
      Serial.print("n00d1b: ");
      Serial.print(n00d1b);
      Serial.print("\t in binary: ");
      Serial.println(n00d1b, BIN);
    }
    if (channelToPrint == 2) // only nood2a
    {
      if (throttle & (0x1 << 7)) // 128
      {
        Serial.print("TX_THROTTLE: ");
        Serial.print(data.ch[TX_THROTTLE]);
        Serial.print("\t throttle: ");
        Serial.print(throttle);
        Serial.print("\t (in binary: ");
        Serial.print(throttle, BIN);
      }
      Serial.print("\t n00d2a: ");
      Serial.print(n00d2a);
      Serial.print("\t in binary: ");
      Serial.println(n00d2a, BIN);
    }
    if (channelToPrint == 3) // only nood2b
    {
      if (throttle & (0x1 << 6)) // 64
      {
        Serial.print("TX_THROTTLE: ");
        Serial.print(data.ch[TX_THROTTLE]);
        Serial.print("\t throttle: ");
        Serial.print(throttle);
        Serial.print("\t (in binary: ");
        Serial.print(throttle, BIN);
      }
      Serial.print("n00d2b: ");
      Serial.print(n00d2b);
      Serial.print("\t in binary: ");
      Serial.println(n00d2b, BIN);
    }
    if (channelToPrint == 100) // everything
    {
      Serial.print("TX_THROTTLE: ");
      Serial.print(data.ch[TX_THROTTLE]);
      Serial.print("\t throttle: ");
      Serial.print(throttle);
      Serial.print("\t (in binary: ");
      Serial.println(throttle, BIN);
      Serial.print("n00d1a: ");
      Serial.print(n00d1a);
      Serial.print("\t n00d1b: ");
      Serial.print(n00d1b);
      Serial.print("\t n00d2a: ");
      Serial.print(n00d2a);
      Serial.print("\t n00d2b: ");
      Serial.println(n00d2b);
      Serial.println("");
    }
  }
}

void checkIncomingSerial()
{
  if (Serial.available() > 0)
  {
    char inChar = Serial.read();
    switch (inChar)
    {
    case '1':
      channelToPrint = 0;
      break;
    case '2':
      channelToPrint = 1;
      break;
    case '3':
      channelToPrint = 2;
      break;
    case '4':
      channelToPrint = 3;
      break;
    case 'a':
      channelToPrint = 100;
      break;
    case 'x':
      channelToPrint = 255;
      break;
    }

    while (Serial.available() > 0)
    {
      Serial.read();
    }
  }
}

void setn00d(uint8_t chan, uint8_t val)
{
  ledcWrite(chan, (255 - val));
}

void parseSBUS(bool serialPrint)
{
  if (sbus_rx.Read())
  {
    sbusPrevPacketTime = millis();
    if (connectionState == CONNECTION_LOST)
    {
      Serial.println("Regained SBUS connection");
      connectionState = CONNECTION_ESTABLISHED;
    }

    /* Grab the received data */
    data = sbus_rx.data();

    /* Display the received data */
    if (millis() - sbusPacketPrintPrevTime > SBUS_PACKET_PRINT_INTERVAL)
    {
      //*
      if (Serial && serialPrint)
      {
        for (int8_t i = 0; i < data.NUM_CH; i++)
        {
          Serial.print(data.ch[i]);
          Serial.print("\t");
        }
        Serial.println();
      }
      //*/

      sbusPacketPrintPrevTime = millis();
    }
  }

  // if SBUS lost, reset the channels
  if (millis() - sbusPrevPacketTime > SBUS_LOST_TIMEOUT)
  {
    if (!connectionState == CONNECTION_LOST)
    {
      Serial.print("Lost SBUS connection >> setting throttle/pitch/roll to ");
      Serial.print((SBUS_VAL_MIN + SBUS_VAL_MAX) / 2);
      Serial.println(" and yaw to 0 ");
      
      connectionState = CONNECTION_LOST;
    }
  }

  if (connectionState == CONNECTION_LOST)
  {
    resetSbusData();
  }
}

void resetSbusData() {
    for (int8_t i = 0; i < data.NUM_CH; i++)
    {
      data.ch[i] = SBUS_VAL_MIN;
      if (i < 4)
      {
        data.ch[i] = (SBUS_VAL_MIN + SBUS_VAL_MAX) / 2;
        if (i == TX_YAW)
          data.ch[i] = SBUS_VAL_MIN;
      }
    }
}

void updateHeadBodyState()
{
  if (data.ch[TX_AUX1] < SBUS_SWITCH_MIN_THRESHOLD)
  {
    headState = STATE_1;
  }
  else
  {
    headState = STATE_2;
  }

  if (data.ch[TX_AUX2] > SBUS_SWITCH_MIN_THRESHOLD)
  {
    bodyState = NOOD1;
  }
  else if (data.ch[TX_AUX2] > SBUS_SWITCH_MAX_THRESHOLD)
  {
    bodyState = NOOD2;
  }
  else
  {
    bodyState = BOTH_NOODS;
  }
}

// led 1 and 3 = eyes
// led 2 = mouth
void updateHeadLighting()
{
  float audioVal = constrain(map(data.ch[TX_YAW], SBUS_VAL_MIN, SBUS_VAL_MAX, 0, 255), 0, 255);
  switch (headState)
  {
  case STATE_1:
    pixels.setPixelColor(0, pixels.Color(audioVal, 255, audioVal));
    pixels.setPixelColor(1, pixels.Color(255, audioVal, audioVal));
    pixels.setPixelColor(2, pixels.Color(audioVal, 255, audioVal));
    break;
  case STATE_2:
    pixels.setPixelColor(0, pixels.Color(audioVal, audioVal, audioVal));
    pixels.setPixelColor(1, pixels.Color(255, audioVal, audioVal));
    pixels.setPixelColor(2, pixels.Color(audioVal, audioVal, audioVal));
    break;
  }
  pixels.show(); // Send the updated pixel colors to the hardware.
}

void calcMotorValues() {
  byte motorPowerRange = 255;
  if (data.ch[TX_AUX4] > SBUS_SWITCH_MIN_THRESHOLD)
  {
    motorPowerRange = 255;
  }
  else if (data.ch[TX_AUX4] > SBUS_SWITCH_MAX_THRESHOLD)
  {
    motorPowerRange = 130;
  }
  else
  {
    motorPowerRange = 80;
  }

  motor1Val = constrain(map(data.ch[TX_ROLL], SBUS_VAL_MIN, SBUS_VAL_MAX, -motorPowerRange, motorPowerRange), -255, 255);
  motor2Val = constrain(map(data.ch[TX_PITCH], SBUS_VAL_MIN, SBUS_VAL_MAX, -motorPowerRange, motorPowerRange), -255, 255);

  doSineMovement = (data.ch[TX_AUX4] < SBUS_SWITCH_MIN_THRESHOLD) ? true : false;
  doSineMovement = false; // override

  int16_t throttleVal = motor2Val;
  EVERY_N_MILLIS(250)
  {
    // Serial.print("motorPowerRange: " + String(motorPowerRange));
    // Serial.println(", throttleVal: " + String(motor2Val));
  }

  // float mix = constrain(map(data.ch[TX_ROLL], SBUS_VAL_MIN, SBUS_VAL_MAX, 0, 1000), 750, 250) / 1000.0; // gives a range of .25-.75

  // /*
  // range 0.0-1.0, then an exponent, then map to 250-750
  float mix = constrain(map(data.ch[TX_ROLL], SBUS_VAL_MIN, SBUS_VAL_MAX, 0, 1000), 0, 1000) / 1000.0; // gives a range of 0-1.0
  // mix = pow(mix, 1.4);
  // mix = map((mix * 1000.0), 1000, 0, 250, 750) / 1000.0; // reverse the input range because we want to reverse the steering
  mix = map((mix * 1000.0), 1000, 0, 0, 1000) / 1000.0; // reverse the input range because we want to reverse the steering
  //*/

  motor1Val = (throttleVal * (1.0 - mix)) * 2;
  motor2Val = (throttleVal * mix) * 2;

  // only applies if doSineMovement is true
  // sinCounterIncrement = map(data.ch[TX_THROTTLE], SBUS_VAL_MIN, SBUS_VAL_MAX, 200, 1000) / 5000.0;
  sinCounterIncrement = 550 / 5000.0; // override for testing
  float sinMulFactor = .9;
  sinMulFactor = constrain(map(data.ch[TX_AUX3], SBUS_VAL_MIN, SBUS_VAL_MAX, 450, 900), 450, 900) / 1000.0;
  float sinMult1 = sin(sinCounter) * sinMulFactor + (1.0 - sinMulFactor);
  float sinMult2 = sin(sinCounter + PI) * sinMulFactor + (1.0 - sinMulFactor);
  sinCounter += sinCounterIncrement;
  // Serial.println("sinCounterIncrement: " + String(sinCounterIncrement));

  if (doSineMovement)
  {
    float ampMul = constrain(map(data.ch[TX_AUX4], SBUS_VAL_MIN, SBUS_VAL_MAX, 0, 1000), 0, 1000) / 1000.0;
    motor1Val *= (sinMult1 * ampMul) + (1.0 - ampMul);
    motor2Val *= (sinMult2 * ampMul) + (1.0 - ampMul);
  }

  motor1Val = constrain(motor1Val, -255, 255);
  motor2Val = constrain(motor2Val, -255, 255);
}


void driveMotors()
{
  // MOTOR 1
  if (abs(motor1Val) < SBUS_VAL_DEADBAND)
  {
    motor1.motorStop(); // Soft Stop    -no argument
  }
  if (motor1Val < -SBUS_VAL_DEADBAND)
  {
    motor1.motorRev(motor1Val); // Pass the speed to the motor: 0-255 for 8 bit resolution
  }
  if (motor1Val > SBUS_VAL_DEADBAND)
  {
    motor1.motorGo(motor1Val); // Pass the speed to the motor: 0-255 for 8 bit resolution
  }

  // MOTOR 2
  if (abs(motor2Val) < SBUS_VAL_DEADBAND)
  {
    motor2.motorStop(); // Soft Stop    -no argument
  }
  if (motor2Val < -SBUS_VAL_DEADBAND)
  {
    motor2.motorRev(motor2Val); // Pass the speed to the motor: 0-255 for 8 bit resolution
  }
  if (motor2Val > SBUS_VAL_DEADBAND)
  {
    motor2.motorGo(motor2Val); // Pass the speed to the motor: 0-255 for 8 bit resolution
  }
}

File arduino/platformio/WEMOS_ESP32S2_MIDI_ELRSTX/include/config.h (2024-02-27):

/*
 * This file is part of Simple TX
 *
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
 * You should have received a copy of the GNU General Public License
 * along with Cleanflight.  If not, see <http://www.gnu.org/licenses/>.
 */

//#define USE_M7

/*
 =======================================================================================================
 Simple TX CONFIG OPTIONS (comment out unneeded options)
 =======================================================================================================
 */
// Define analogy input limite

#include <Arduino.h>

// #define ADC_MIN 0
// #define ADC_MID 511
// #define ADC_MAX 1023
#define ADC_MIN 0
#define ADC_MID 4095
#define ADC_MAX 8191


#define ANALOG_CUTOFF 150 // cut off lower and upper end to avoid un-symmetric joystick range in trade off resolution

// Define RC input Offset
#ifdef USE_M7
// M7
int Aileron_OFFSET    = -46;
int Elevator_OFFSET   = 57;
int Throttle_OFFSET   = 0;
int Rudder_OFFSET     = -18;
#else
// stat war
int Aileron_OFFSET    = 0;
int Elevator_OFFSET   = 0;
int Throttle_OFFSET   = 0;
int Rudder_OFFSET     = 0;
#endif

// Define Reverse 1=reverse
int Is_Aileron_Reverse  =1;
int Is_Elevator_Reverse =0;
int Is_Throttle_Reverse =1;
int Is_Rudder_Reverse   =0;

// IO setup
// pins that used for the Joystick
const int analogInPinAileron = 5;
const int analogInPinElevator = 7;
const int analogInPinThrottle = 3;
const int analogInPinRudder = 9;
const int VOLTAGE_READ_PIN = 11;

// pins that used for the switch
const int DIGITAL_PIN_SWITCH_ARM = 1;  // Arm switch
const int DIGITAL_PIN_SWITCH_AUX2 = 2; //
const int DIGITAL_PIN_SWITCH_AUX3 = 4;  //
// const int DIGITAL_PIN_SWITCH_AUX4 = 5;  //

// pins that used for output
const int DIGITAL_PIN_LED = LED_BUILTIN;    // in pcb v0.9 led is reused from AUX4 (remember to add 300om resistor in led)
//const int DIGITAL_PIN_BUZZER = 7; // do not use in pcb v0.9

// pins that used for buzzer
const int DIGITAL_PIN_BUZZER = 6;
//----- Voltage monitoring -------------------------
// Define battery warning voltage
const float WARNING_VOLTAGE = 7.4; // 2S Lipo 3.7v per cell
const float BEEPING_VOLTAGE = 7.0; // 2S Lipo 3.5v per cell

// Define Commond for start Up Setting
#define RC_MIN_COMMAND 600
#define RC_MAX_COMMAND 1400

// Define stick unmove alarm time
#define STICK_ALARM_TIME 30000

// from https://github.com/DeviationTX/deviation/pull/1009/ ELRS menu implement in deviation TX
/*static uint8_t  currentPktRate =1; //  "250Hz", "150Hz", "50Hz"
  //                                       1        3       5
static uint8_t  currentPower =1 ;//  "10mW", "25mW", "50mW", "100mW", "250mW"
  //                                   0     1         2        3        4
*/
// ELRS 2.0:
//  1 : Set Lua [Packet Rate]= 0 - 50Hz / 1 - 150Hz / 3 - 250Hz
//  2 : Set Lua [Telem Ratio]= 0 - off / 1 - 1:128 / 2 - 1:64 / 3 - 1:32 / 4 - 1:16 / 5 - 1:8 / 6 - 1:4 / 7 - 1:2
//  3 : Set Lua [Switch Mode]=0 -> Hybrid;Wide
//  4 : Set Lua [Model Match]=0 -> Off;On
//  5 : Set Lua [TX Power]=0 - 10mW / 1 - 25mW / 2 - 50mW /3 - 100mW/4 - 250mW
// 3 Default Settings
#define SETTING_1_PktRate 2 // 250Hz
#define SETTING_1_Power 1   // 25mW

#define SETTING_2_PktRate 1 // 150Hz
#define SETTING_2_Power 3   // 100mW

#define SETTING_3_PktRate 3 // 500Hz
#define SETTING_3_Power 1   // 25mW

enum chan_order
{
    AILERON,
    ELEVATOR,
    THROTTLE,
    RUDDER,
    AUX1, // (CH5)  ARM switch for Expresslrs
    AUX2, // (CH6)  angel / airmode change
    AUX3, // (CH7)  flip after crash
    AUX4, // (CH8)
    AUX5, // (CH9)
    AUX6, // (CH10)
    AUX7, // (CH11)
    AUX8, // (CH12)
};

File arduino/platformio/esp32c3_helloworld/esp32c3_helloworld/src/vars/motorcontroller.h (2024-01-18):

#define PIN_MOTOR1_A D5
#define PIN_MOTOR1_B D4
#define CH_MOTOR1_1 2 // 16 Channels (0-15) are availible
#define CH_MOTOR1_2 3 // Make sure each pin is a different channel and not in use by other PWM devices (servos, LED's, etc)

#define PIN_MOTOR2_A D3
#define PIN_MOTOR2_B D2
#define CH_MOTOR2_1 4 // 16 Channels (0-15) are availible
#define CH_MOTOR2_2 5 // Make sure each pin is a different channel and not in use by other PWM devices (servos, LED's, etc)

// Optional Parameters
#define RES 8     // Resolution in bits:  8 (0-255),  12 (0-4095), or 16 (0-65535)
#define FREQ 5000 // PWM Frequency in Hz

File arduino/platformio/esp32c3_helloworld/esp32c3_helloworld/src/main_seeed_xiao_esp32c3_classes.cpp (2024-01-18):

#include <Arduino.h>
#include <ESP32MX1508.h>
#include <Adafruit_BusIO_Register.h>
#include "sbus.h"
#include <HardwareSerial.h>
#include <Adafruit_NeoPixel.h>
#include <FastLED.h>

// variables
#include "vars/motorcontroller.h"
#include "vars/neopixels.h"
#include "vars/sbusrx.h"


// When setting up the NeoPixel library, we tell it how many pixels,
// and which pin to use to send signals. Note that for older NeoPixel
// strips you might need to change the third parameter -- see the
// strandtest example for more information on possible values.
Adafruit_NeoPixel pixels(NUMPIXELS, PIN, NEO_GRB + NEO_KHZ800);

/* SBUS object, reading SBUS */
bfs::SbusRx sbus_rx(&MySerial0, D7, D6, true, false);

MX1508 motorA(PIN_MOTOR1_A, PIN_MOTOR1_B, CH_MOTOR1_1, CH_MOTOR1_2, RES, 2500); // Default-  8 bit resoluion at 2500 Hz
MX1508 motorB(PIN_MOTOR2_A, PIN_MOTOR2_B, CH_MOTOR2_1, CH_MOTOR2_2, RES, 2500); // Default-  8 bit resoluion at 2500 Hz

float sinCounter = 0.0;
float sinCounterIncrement = 0.05;

bool doSineMovement = false;

byte hVal = 0;
byte vVal = 0;

void setup()
{
  Serial.begin(115200);

  /* Begin the SBUS communication */
  sbus_rx.Begin();
  // sbus_tx.Begin();

  // by default, let's have the program assume sbus is lost
  sbusPrevPacketTime = -SBUS_LOST_TIMEOUT;

  pixels.begin(); // INITIALIZE NeoPixel strip object (REQUIRED)

  Serial.println("Hello World!");
}

void loop()
{
  // pixels.clear(); // Set all pixel colors to 'off'

  // read SBUS
  if (sbus_rx.Read())
  {
    sbusPrevPacketTime = millis();
    if (sbusLost)
    {
      Serial.println("Regained SBUS connection");
      sbusLost = false;
    }

    /* Grab the received data */
    data = sbus_rx.data();

    /* Display the received data */
    if (millis() - sbusPacketPrintPrevTime > SBUS_PACKET_PRINT_INTERVAL)
    {
      if (Serial)
      {
        for (int8_t i = 0; i < data.NUM_CH; i++)
        {
          Serial.print(data.ch[i]);
          Serial.print("\t");
        }
        Serial.println();
      }

      sbusPacketPrintPrevTime = millis();
    }
  }

  // if SBUS lost, reset the channels
  if (millis() - sbusPrevPacketTime > SBUS_LOST_TIMEOUT)
  {
    if (!sbusLost)
    {
      Serial.print("Lost SBUS connection >> setting first 4 channels to ");
      Serial.println((SBUS_VAL_MIN + SBUS_VAL_MAX) / 2);
      sbusLost = true;
    }
  }

  if (sbusLost)
  {
    for (int8_t i = 0; i < data.NUM_CH; i++)
    {
      data.ch[i] = SBUS_VAL_MIN;
      if (i < 4)
      {
        data.ch[i] = (SBUS_VAL_MIN + SBUS_VAL_MAX) / 2;
      }
    }
  }

  byte motorPowerRange = 50;
  if (data.ch[TX_AUX2] > SBUS_SWITCH_MAX_THRESHOLD) {
    motorPowerRange = 50;
  } else if (data.ch[TX_AUX2] > SBUS_SWITCH_MIN_THRESHOLD) {
    motorPowerRange = 35;
  } else {
    motorPowerRange = 20;
  }

  int16_t motor1Val = constrain(map(data.ch[TX_ROLL], SBUS_VAL_MIN, SBUS_VAL_MAX, -motorPowerRange, motorPowerRange), -255, 255);
  int16_t motor2Val = constrain(map(data.ch[TX_PITCH], SBUS_VAL_MIN, SBUS_VAL_MAX, -motorPowerRange, motorPowerRange), -255, 255);

  // hVal = constrain(map(data.ch[TX_YAW], SBUS_VAL_MIN, SBUS_VAL_MAX, 0, 250), 0, 250);
  hVal = constrain(map(data.ch[TX_YAW], SBUS_VAL_MIN, SBUS_VAL_MAX, 0, 250), 0, 250);
  vVal = constrain(map(data.ch[TX_THROTTLE], SBUS_VAL_MIN, SBUS_VAL_MAX, 0, 225), 0, 225);

  //*
  // sets variable hVal according to position of tx_aux1
  if (data.ch[TX_AUX1] < SBUS_SWITCH_MIN_THRESHOLD)
  {
    // Serial.println("lock in hue val");
    hVal = 32;
    // hVal = 32;
  }
  //*/

  for (int i = 0; i < NUMPIXELS; i++)
  {
    pixels.setPixelColor(i, pixels.Color(hVal, 0, 25 + vVal));
  }
  pixels.show(); // Send the updated pixel colors to the hardware.
  // for (int i = 0; i < NUM_LEDS; i++)
  // {
  //   leds[i] = CHSV(hVal, 240, 25 + vVal);
  // }
  // FastLED.show();

  doSineMovement = (data.ch[TX_AUX4] < SBUS_SWITCH_MIN_THRESHOLD) ? true : false;

  int16_t throttleVal = motor2Val;
  float mix = constrain(map(data.ch[TX_ROLL], SBUS_VAL_MIN, SBUS_VAL_MAX, 0, 1000), 250, 750) / 1000.0; // gives a range of .25-.75
  motor1Val = (throttleVal * (1.0 - mix)) * 2;
  motor2Val = (throttleVal * mix) * 2;

  sinCounterIncrement = map(data.ch[TX_THROTTLE], SBUS_VAL_MIN, SBUS_VAL_MAX, 200, 1000) / 5000.0;
  float sinMult1 = (sin(sinCounter) + 1.0);
  float sinMult2 = (sin(sinCounter + HALF_PI) + 1.0);
  sinCounter += sinCounterIncrement;
  // Serial.println("sinCounterIncrement: " + String(sinCounterIncrement));

  if (doSineMovement)
  {
    motor1Val *= (sinMult1 *.75) + .25;
    motor2Val *= (sinMult2 *.75) + .25;
  }

  motor1Val = constrain(motor1Val, -255, 255);
  motor2Val = constrain(motor2Val, -255, 255);

  // MOTOR 1
  if (abs(motor1Val) < SBUS_VAL_DEADBAND)
  {
    motorA.motorStop(); // Soft Stop    -no argument
  }
  if (motor1Val < -SBUS_VAL_DEADBAND)
  {
    motorA.motorRev(-motor1Val); // Pass the speed to the motor: 0-255 for 8 bit resolution
  }
  if (motor1Val > SBUS_VAL_DEADBAND)
  {
    motorA.motorGo(motor1Val); // Pass the speed to the motor: 0-255 for 8 bit resolution
  }

  // MOTOR 2
  if (abs(motor2Val) < SBUS_VAL_DEADBAND)
  {
    motorB.motorStop(); // Soft Stop    -no argument
  }
  if (motor2Val < -SBUS_VAL_DEADBAND)
  {
    motorB.motorRev(-motor2Val); // Pass the speed to the motor: 0-255 for 8 bit resolution
  }
  if (motor2Val > SBUS_VAL_DEADBAND)
  {
    motorB.motorGo(motor2Val); // Pass the speed to the motor: 0-255 for 8 bit resolution
  }

  // delay a little.
  delay(1000 / 200);
}

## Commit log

2023-12-13 first commit of esp32-c3 pio project
2023-12-13 expand to 2 motor control
2023-12-14 implement correct rx control mapping to motors
    [main_seeed_xiao_esp32c3.cpp]
2023-12-15 add a few test sketches to research a led flickering control issue
    [main_ledcontrol_sbuscontrol.cpp]
2023-12-15 add Teensy project (doesn't work yet)
    [main.cpp]
2024-01-18 add Teensy breakout board PCB
    [Teensy_32_tx_breakout_board.csv, Teensy_32_tx_breakout_board.kicad_pcb, Teensy_32_tx_breakout_board.kicad_sch]
2024-01-18 add xiao esp32c3 project (so far)
2024-01-18 add some Teensy code
2024-02-03 add xiao esp32c3 footprint
2024-02-03 create teensy breakout v2
    [Teensy_32_tx_breakout_board_v2.csv, Teensy_32_tx_breakout_board_v2.kicad_pcb, Teensy_32_tx_breakout_board_v2.kicad_sch]
2024-02-03 add a few pcb gfx
2024-02-03 add footprints for head pcb
2024-02-03 create symbols for head pcb
2024-02-03 create actual v1 of head pcb
    [eel_head_pcbs_assembly_v01.kicad_pcb, eel_head_pcbs_assembly_v01.kicad_sch]
2024-02-03 create v2 of head pcb
    [eel_head_pcbs_assembly_v02.kicad_pcb, eel_head_pcbs_assembly_v02.kicad_sch]
2024-02-03 create v3 of head pcb
    [eel_head_pcbs_assembly_v03.kicad_pcb, eel_head_pcbs_assembly_v03.kicad_sch]
2024-02-03 create teensy test sketch - midi directly to buitlin-led
2024-02-03 update teensy main sketch
2024-02-20 test: address motors directly with ledcWrite
2024-02-20 debug sketch: test motor control with new class
2024-02-20 test sketch: sbus-receive signals and translate to n00ds ledc out
2024-02-20 test sketch: add one motor with direct ledcWrite
2024-02-20 test sketch: address two motors with new external class
2024-02-20 test sketch: locally control n00ds with direct ledcWrite
2024-02-23 create custom footprints
2024-02-29 fix motor reverse error
    [eel_with_lightcontrol_04_2_motors_classes.cpp]
2024-02-29 fix motor direction bug
    [main_seeed_xiao_esp32c3.cpp]
2024-02-29 move motor vals calc to its own method
2024-03-07 update 3d model references for footprints
2024-03-07 update xiao pcb
    [eel_esp32_switch_host_board_v02.kicad_pcb, eel_esp32_switch_host_board_v02.kicad_sch]
2024-03-07 fix incorrect 'motor reverse' approach
2024-04-03 Separated motor mount
    [Motor Mount.3mf]
2024-04-03 Add mouth light guide multi material
    [Mouth Light Guide.3mf]
2024-04-03 Deeper motor mount grooves
    [Motor Mount.3mf]
2024-04-03 Add Switch cap
    [Switch cap .3mf]
2024-04-03 Switch cap to fine
    [Switch cap .3mf]
2024-04-10 Increase quality with wall thickness
    [Head Upper.3mf]
2024-04-10 Reduce motor mount ridge height
    [Head Upper.3mf]
2024-04-17 Update BOM with extra n00d segment
2024-11-13 Add eye light guide
    [Eye Light Guide.3mf]
2025-11-13 Add CAD source files
    [Eye Light Guide.3mf, Haribo.step, Head Lower.3mf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]
2025-11-18 move interactive BOM
2025-11-19 add organized exported pcb/schematic assets
2025-11-19 organize exported assets of some of the Kicad projects
2025-11-19 update Arduino README

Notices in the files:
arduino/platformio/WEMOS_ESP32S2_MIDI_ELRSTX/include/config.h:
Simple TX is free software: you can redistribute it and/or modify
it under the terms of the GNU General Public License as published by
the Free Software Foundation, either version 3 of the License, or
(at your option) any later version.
